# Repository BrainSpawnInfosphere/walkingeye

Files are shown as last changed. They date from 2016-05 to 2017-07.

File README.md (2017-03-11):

# XL-320 Quadruped





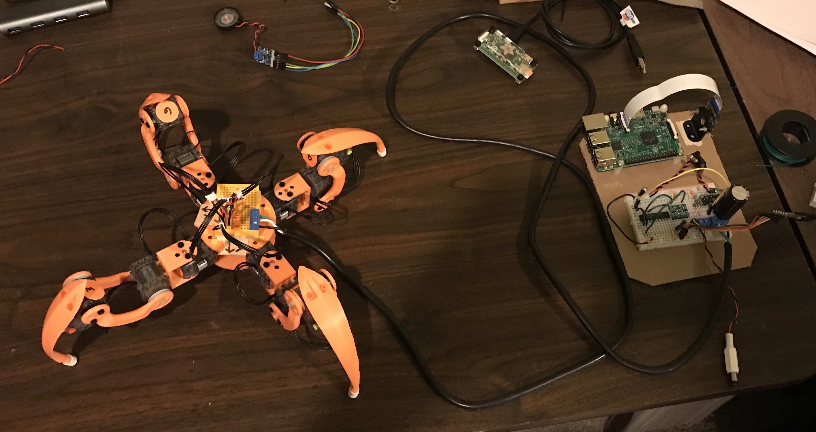
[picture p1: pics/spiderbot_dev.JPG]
spidebot dev


This is my second one after the RC version, which didn't work as nicely as I
wanted it too.

Inspired by the original [Walking Eye](https://www.youtube.com/watch?v=f77gw2Pp3aY)

## Videos

* [YouTube](https://www.youtube.com/watch?v=kH2hlxUfCNg)
* [Vimeo](https://player.vimeo.com/video/194676675)

**Still a work in progress**

## Current Pics

**As of 2017 Feb 26**

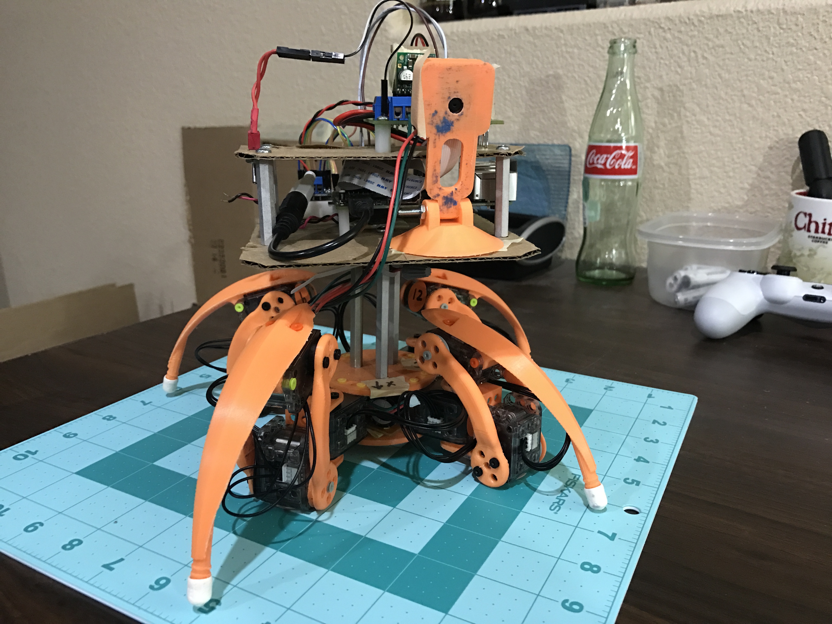
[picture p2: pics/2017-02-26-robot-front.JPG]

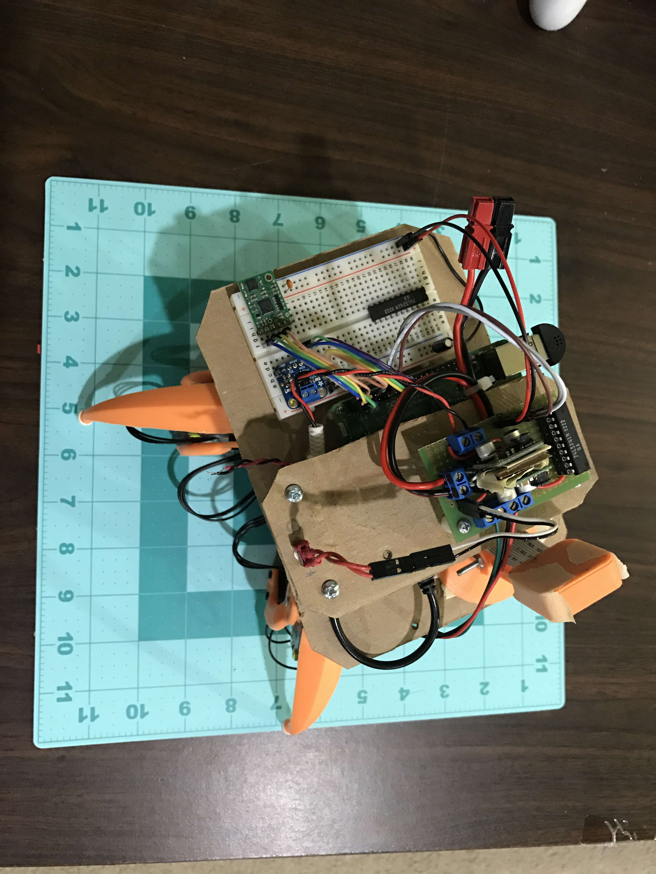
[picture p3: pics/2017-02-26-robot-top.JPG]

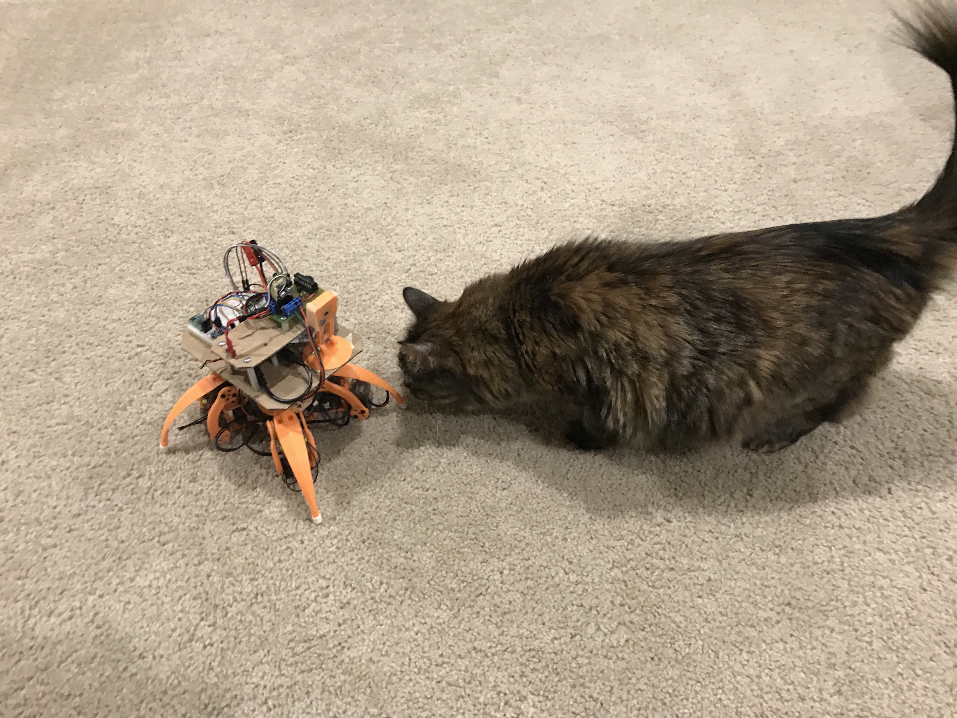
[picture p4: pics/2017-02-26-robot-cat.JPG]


Between the mat with a grid in inches and my cat, you can get an idea of the size.

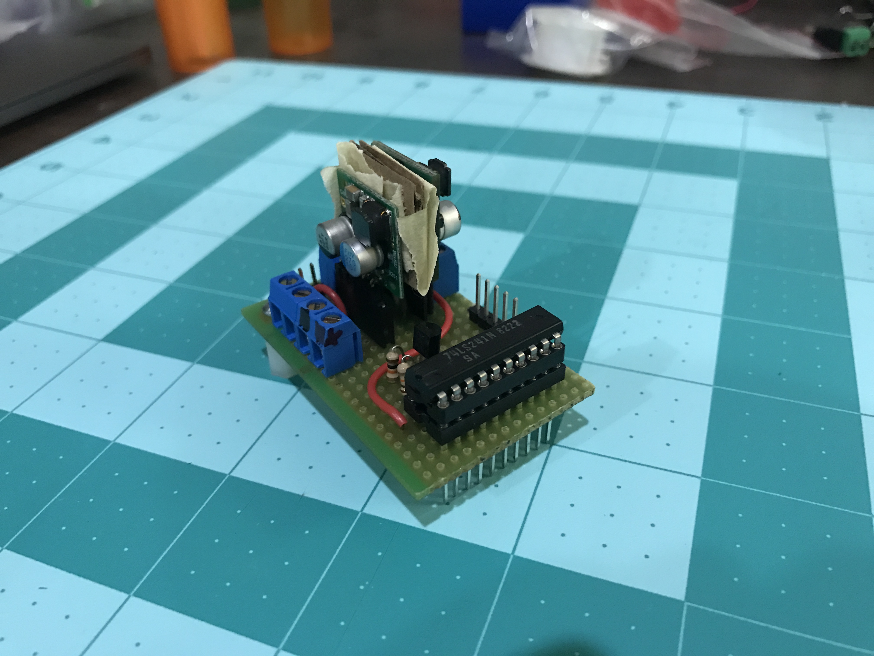
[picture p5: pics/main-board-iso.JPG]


The 2 buck converts (5V and 7.5V) were really close to each other, so I stuck a piece of cardboard between them. To prevent the cardboard from slipping, I also used some tape to hold them in place. I will eventaully turn this into a real PCB once I am fully happy with it and do a better layout.

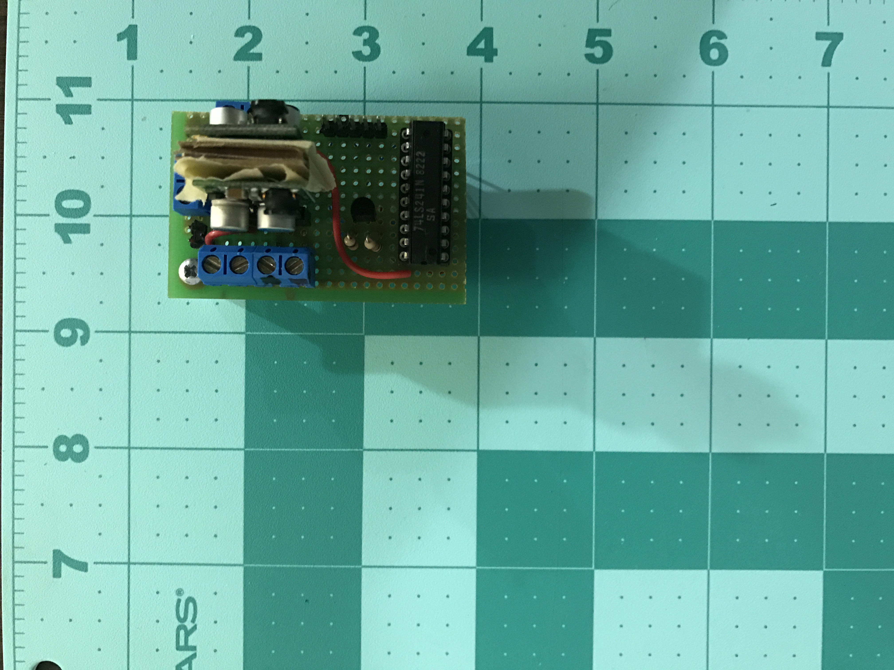
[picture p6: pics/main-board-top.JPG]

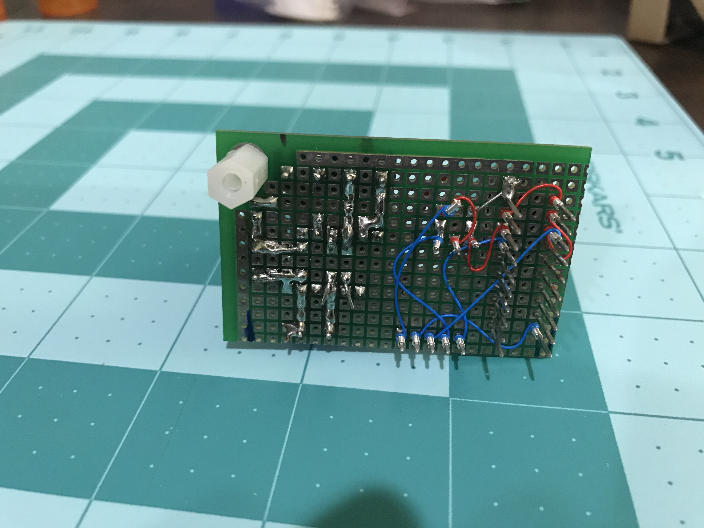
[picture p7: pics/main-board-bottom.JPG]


Decent job of soldering and wire wrapping, however, the scrap of protoboard I was useing only had 1 mounting hole to put a nylon stand off in. So far the single mount point doesn't seem to be an issue.

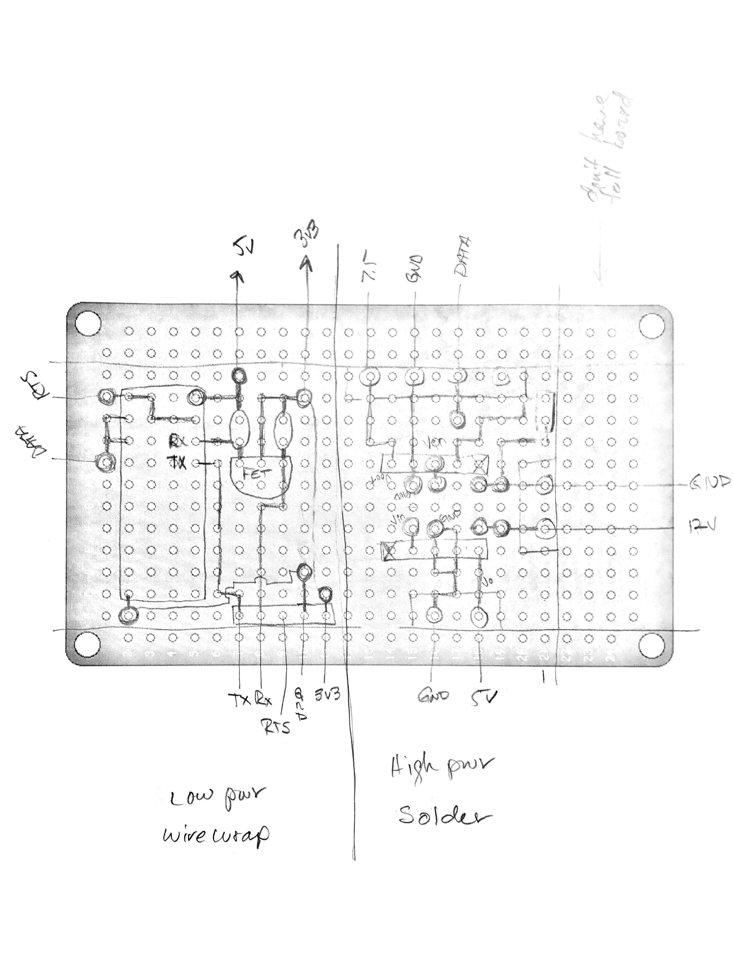
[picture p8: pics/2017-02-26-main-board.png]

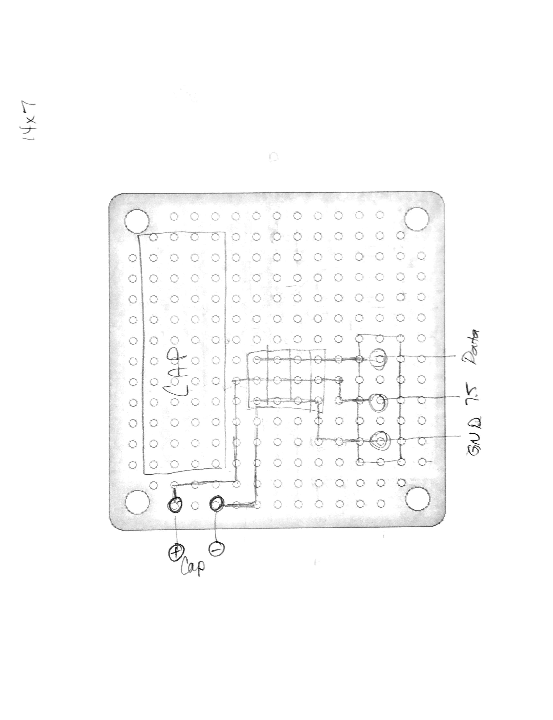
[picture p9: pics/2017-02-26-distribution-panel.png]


My hand drawn circuit diagrams using some protoboard pictures I found on the internet. I will eventually turn these into PCB's and post the schematics (probably going to use EagleCAD since it is free).

## Documentation

- [Markdown](./docs/Markdown)
- [Jupyter Notebooks](./docs/ipython)

# Licenses

**Note:** The software, hardware, and documentation are under different licenses.

## Software

**The MIT License (MIT)**

Copyright (c) 2016 Kevin J. Walchko

Permission is hereby granted, free of charge, to any person obtaining a copy of
this software and associated documentation files (the "Software"), to deal in
the Software without restriction, including without limitation the rights to
use, copy, modify, merge, publish, distribute, sublicense, and/or sell copies
of the Software, and to permit persons to whom the Software is furnished to do
so, subject to the following conditions:

The above copyright notice and this permission notice shall be included in all
copies or substantial portions of the Software.

THE SOFTWARE IS PROVIDED "AS IS", WITHOUT WARRANTY OF ANY KIND, EXPRESS OR
IMPLIED, INCLUDING BUT NOT LIMITED TO THE WARRANTIES OF MERCHANTABILITY, FITNESS
FOR A PARTICULAR PURPOSE AND NONINFRINGEMENT. IN NO EVENT SHALL THE AUTHORS OR
COPYRIGHT HOLDERS BE LIABLE FOR ANY CLAIM, DAMAGES OR OTHER LIABILITY, WHETHER
IN AN ACTION OF CONTRACT, TORT OR OTHERWISE, ARISING FROM, OUT OF OR IN
CONNECTION WITH THE SOFTWARE OR THE USE OR OTHER DEALINGS IN THE SOFTWARE.

## Hardware and Documentation

<p align="center">
	<a rel="license" href="http://creativecommons.org/licenses/by-sa/4.0/">
		
	</a>
	<br />This work is licensed under a <a rel="license" href="http://creativecommons.org/licenses/by-sa/4.0/">Creative Commons Attribution-ShareAlike 4.0 International License</a>.
</p>

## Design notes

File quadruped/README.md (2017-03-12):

# Software

**Issue:** Anything that has opencv in it *can't* be derived from `process`, opencv
crashes. It has to be in it's own python script *or* be derived from `object`.

Simple layout of the code:

- ImageServer:
	- allows image processing to be done off-board
		- allows commands to also come from a completely different type of input
		(joystick) without robot modification
	- grabs image
	- searches for:
		- tennis ball
		- people's faces
	- publishes:
		- images
		- commands to robot

- Audio:
	- listen for speach
	- convert to wave format
	- send to service (wit or whatever)
	- 

- Quadruped:
	- Engine({serial})
	- AHRS() - compass
	- MCP3208() - ADC for IR and whatever else
	- movement_states['walk', 'climb', 'animate', 'sit', 'stand']
		- these are used to call movements[] functions using command()
	- movements[]
		- Gait:
			- command(x, func_move_foot) - moves all feet through 1 gait cycle (12 steps)
			- eachLeg(x,y,z)
		- Pose:
			- command(func_move_foot) - sends all feet through an animation sequence to final position
			- eachLeg(x,y,z)

- Engine({serial}): - handles movement hardware
	- legs[4]
		- servos[3]
			- angle
			- setServoLimits()
			- bulkWrite() - change to sync
		- coxa, femur, tibia
		- fk()
		- ik()
		- moveFoot(x,y,z)
		- moveFootAngle(a,b,c)
	- moveFoot(x,y,z) - gaits need a function to call

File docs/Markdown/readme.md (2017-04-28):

# Documentation

**This is still a work in progress**

This documentation is broken up into two types:

- Static markdown files
- Interactive python files (Jupyter notebooks)

Since the software is written in python, iPhython (or now
[Jupyter](http://jupyter.org/)) is used for interactive documentation. Take a
look at the [docs](https://github.com/walchko/WalkingEye/tree/master/docs/ipython)
folder. The ipython files are where some of the development (e.g., gait,
forward/inverse kinematics, etc) takes place before it is tranferred into the
python code.

When viewing the notebooks on `github.com`, they are static, but if you download
them and have Jupyter installed, they are interactive and pretty cool.

## Index

- [Software](./software.md)
- [Hardware](./bom.md)
- [Power](./power.md)
- [History](./history.md)

---

<p align="center">
	<a rel="license" href="http://creativecommons.org/licenses/by-sa/4.0/">
		
	</a>
	<br />This work is licensed under a <a rel="license" href="http://creativecommons.org/licenses/by-sa/4.0/">Creative Commons Attribution-ShareAlike 4.0 International License</a>.
</p>

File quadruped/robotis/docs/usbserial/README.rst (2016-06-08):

USB Serial
=============



RPi v3: ``/dev/tty.????``
OSX: ``/dev/tty.usbserial``

PmodUSBUART Pinout
-------------------------

=== ====== ===========================
Pin Signal Description
=== ====== ===========================
1   RTS    Ready to Send
2   RXD    Receive
3   TXD    Transmit
4   CTS    Clear to Send
5   GND    Ground
6   3V3    Power
=== ====== ===========================

Other
----------

=== === ======================================================

=== === ======================================================
JP1 SYS Powered by FTDI chip, supplies power to remote board
JP1 LCL If remote board is powered, use this setting
LED 1   Data transfer from host computer USB to UART
LED 2   Data transfer from UART to host computer USB
=== === ======================================================

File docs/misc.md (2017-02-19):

Name:   mcp23017
Info:   Configures the MCP23017 I2C GPIO expander
Load:   dtoverlay=mcp23017,<param>=<val>
Params: gpiopin                 Gpio pin connected to the INTA output of the
                                MCP23017 (default: 4)

        addr                    I2C address of the MCP23017 (default: 0x20)

Name:   i2s-gpio28-31
Info:   move I2S function block to GPIO 28 to 31
Load:   dtoverlay=i2s-gpio28-31
Params: <None>

Name:   i2c1-bcm2708
Info:   Enable the i2c_bcm2708 driver for the i2c1 bus
Load:   dtoverlay=i2c1-bcm2708,<param>=<val>
Params: sda1_pin                GPIO pin for SDA1 (2 or 44 - default 2)
        scl1_pin                GPIO pin for SCL1 (3 or 45 - default 3)
        pin_func                Alternative pin function (4 (alt0), 6 (alt2) -
                                default 4)

Name:   i2c-rtc
Info:   Adds support for a number of I2C Real Time Clock devices
Load:   dtoverlay=i2c-rtc,<param>=<val>
Params: ds1307                  Select the DS1307 device

        ds1339                  Select the DS1339 device

        ds3231                  Select the DS3231 device

        mcp7940x                Select the MCP7940x device

        mcp7941x                Select the MCP7941x device

        pcf2127                 Select the PCF2127 device

        pcf8523                 Select the PCF8523 device

        pcf8563                 Select the PCF8563 device

        trickle-resistor-ohms   Resistor value for trickle charge (DS1339-only)

        wakeup-source           Specify that the RTC can be used as a wakeup
                                source

Name:   i2c-pwm-pca9685a
Info:   Adds support for an NXP PCA9685A I2C PWM controller on i2c_arm
Load:   dtoverlay=i2c-pwm-pca9685a,<param>=<val>
Params: addr                    I2C address of PCA9685A (default 0x40)

Name:   i2c-mux
Info:   Adds support for a number of I2C bus multiplexers on i2c_arm
Load:   dtoverlay=i2c-mux,<param>=<val>
Params: pca9542                 Select the NXP PCA9542 device

        pca9545                 Select the NXP PCA9545 device

        pca9548                 Select the NXP PCA9548 device

        addr                    Change I2C address of the device (default 0x70)

Name:   i2c-gpio
Info:   Adds support for software i2c controller on gpio pins
Load:   dtoverlay=i2c-gpio,<param>=<val>
Params: i2c_gpio_sda            GPIO used for I2C data (default "23")

        i2c_gpio_scl            GPIO used for I2C clock (default "24")

        i2c_gpio_delay_us       Clock delay in microseconds
                                (default "2" = ~100kHz)

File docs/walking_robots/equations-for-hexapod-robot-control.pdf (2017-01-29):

Equations for hexapod robot control | www.hexapod-kit.com

# Equations for Hexapod robot control

Determine joints angles according to the position of leg tip. A method for linear interpolation (straight walk).
A method for circular interpolation (curved walk).
A method for body inclination (tilt).

Determine joints angles according to the position of leg tip.

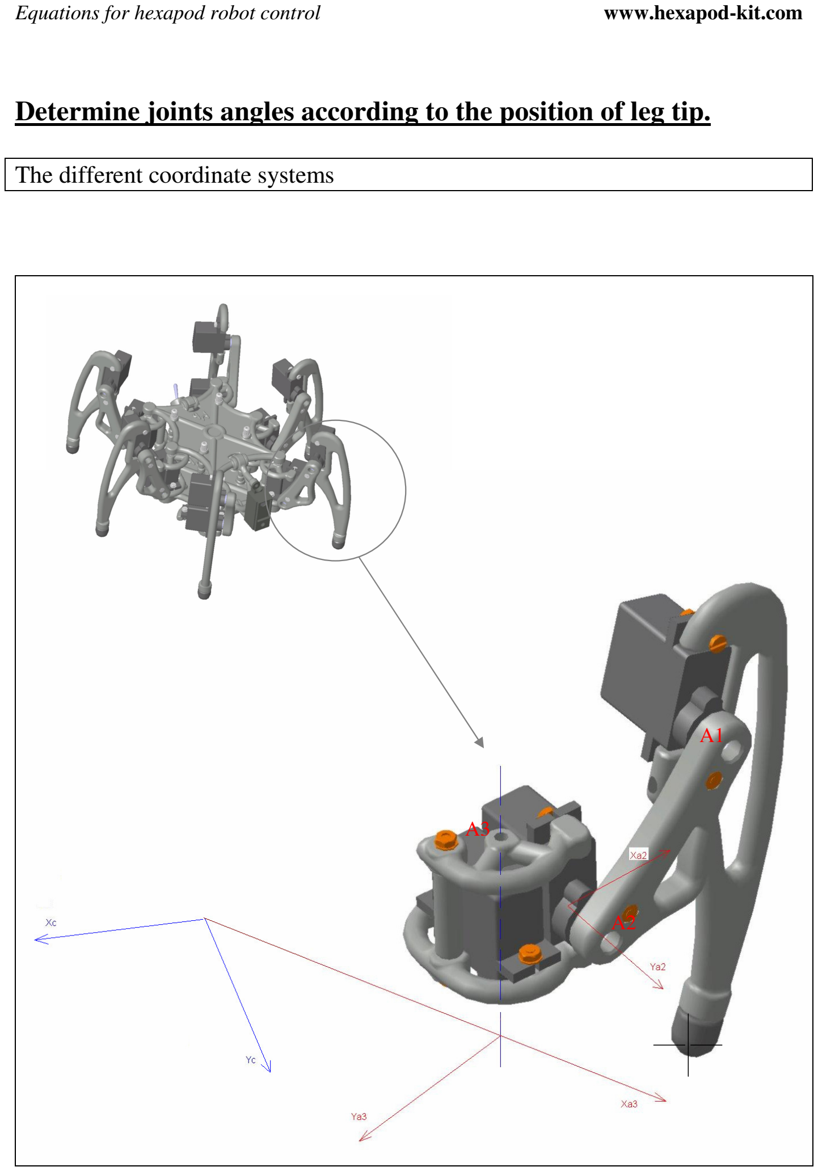
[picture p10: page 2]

The different coordinate systems

A1

A2

A3

We want to drive the tip of a leg by its coordinates in a Cartesian coordinate system.
For reasons of simplicity, we express the coordinates in a fixed coordinate system centred on the body of the hexapod.
To calculate the angles to be applied to the three joints of the leg we have to use different coordinate systems, either fixed or movable relative to the body.
All angle measurements in formulas are expressed in radians.
- Coordinate systems fixed to the body c et a3 :

Seen from above

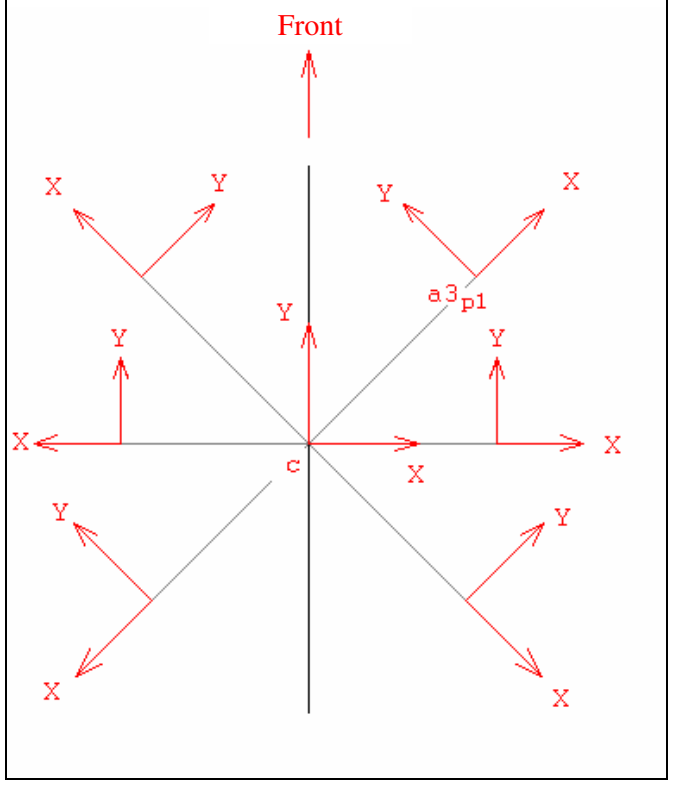
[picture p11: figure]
Front

System c is centred on the robot body. The plan [XY] of the system coincides with the underside of the body (the lowest point).
Systems a3px are centred on A3 joints of each leg.

- Coordinate systems movable relative to the body a2:

Seen top

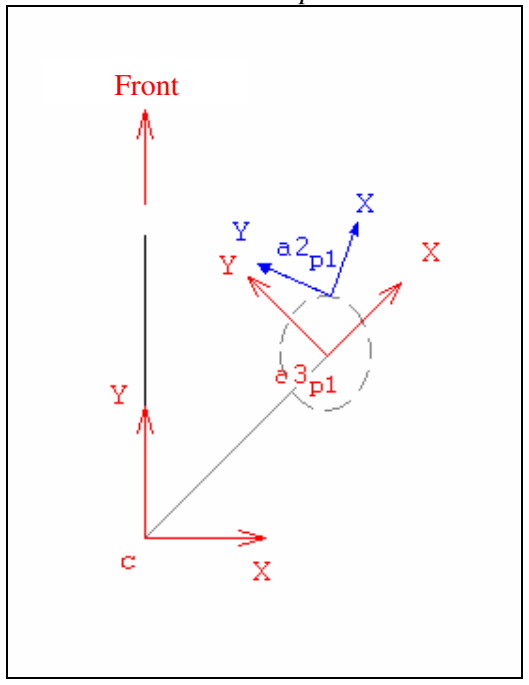
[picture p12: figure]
Front

Joints A2 and A1 in the [XZ] plan of coordinate system a2 :

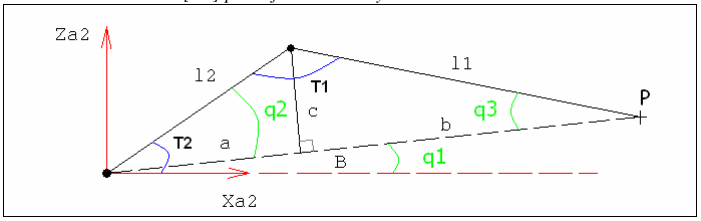
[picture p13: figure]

Given :

- l1et l2 respectively the lengths of the extreme and middle phalanxes.
- T1 angle between the extreme phalanx and middle phalanx.
- T2 angle between X axis and the middle phalanx.
- q1 angle between the axis X and B imaginary line passing through the joint centre A2 and the point P.
- q2 angle between B and the middle phalanx.
- q3 angle between B and the extreme phalanx.

B = a + b
2 | 2 | 2 B = Pxa2 + Pza2

2

cos( )2
l

a
q =

T 2 = q1+ q2

Find T2

B

B | l | l
a
B | aB | l | l
a | B | a | aB | l | l
a | B a | l | l
a | b | l | l
b | l | c
a | l | c

2

2 1

2 | 2 | 1
( | 2 | ) | 2 | 1
( | ) | 2 | 1

2 1

1

2

2 | 2 | 2
2 | 2 | 2
2 | 2 | 2 | 2 | 2
2 | 2 | 2 | 2
2 | 2 | 2 | 2
2 | 2 | 2
2 | 2 | 2
+ | −
=
− | + | = | −
− | + | − | = | −
− | − | = | −
− | = | −
= | −
= | −
l | B
B | l | l
q
2* 2*

2 1
cos( )2
2 | 2 | 2
+ | −
= | )
2

2
) arctan(
2* 2*

2 1

### 2 arccos(

2 | 2 | 2

Pxa

Pza
l | B
B | l | l
T | +
+ | −
=

)
2

2

### 1 arctan(

Pxa

Pza
q =

B

B | l | l
a
| 2 | 2 1
2 | 2 | 2
+ | −
=

cos(a −b) = cos(a)cos(b) + sin(a)sin(b)

Find T1

2 1 2

2 1
2 1 2
2 2 | 2 | 1
cos( )1
| | 2 1 2 2 2
2 1 2
| 2 1
cos( )1

1 2 1 2

2
1 2

2
cos( )1

1 2

2 | ( ( | ))
2
2 | ( | )
cos( )1

1 2

2
1 2

cos( )1

1 1 2

*
2

cos( )1

1 1 2

*
2

cos( )1

1 1 2

1
*
2

2
cos( )1

1 1 2

* 1
2

cos( )1 1

1 2

))
1

*) arcsin(
2

cos( )1 cos(arcsin(

)
1

) arcsin(
2

### 1 arcsin(

) )
1

) arcsin(
2

1 ( arcsin(

)
1

) arccos(
2

### 1 arccos(

1 | 2 | 3
2 | 2 | 2 | 2 | 2 | 2 | 2
2 | 2 | 2 | 2

2 2

2

2

2 2

2 | 2 | 2

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
l | l | B
l l
l | B | l | l
T

ll

l
ll
B | l | l
T

ll

aB
ll

l
ll

l aB T

ll

l a a b
l
l | a | ab T

ll

l | a | ab
ll

c ab T

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
T | q | q
+ | −
=
− | − | +
=
| | +
+ | −
= −
= | −
− | +
= −
− | + | +
= −

− −
=

− +
=

+
=
= | +
= | +

+

− | −
=
= | − | − | +
= | +
= | −
= | − − | + | +
= | − | −
= | − | −
π | π

π

π

)
2 1 2

1 2

### 1 arccos(

2 | 2 | 2

l l

l | l | B
T

+ −
=

Find joint angle A3 (T3)

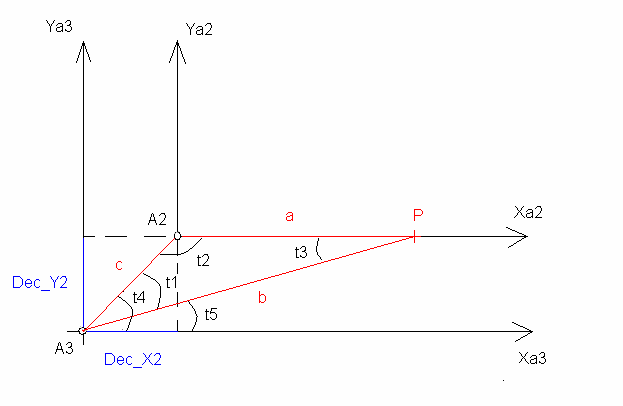
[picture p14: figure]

- Dec_X2 is the offset on X axis, between joints A3 et A2.
- Dec_Y2 is the offset on Y axis, between joints A3 et A2.
- Dec_Z2 is the offset on Z axis, between joints A3 et A2 (=0).
- Given a the projection on Xa2 of the imaginary line B (seen previously).

2 2

2 2

3 3

)
_ 2

_ 2
arctan(
2

2

_ 2 | _ 2
b | Pxa | Pya Dec Y

Dec X
t
c | Dec X | Dec Y
= | +
= | +
= | +

π

We know that :

sin( )1 | sin( )2 | sin(t )3 c
| t

b
t

a
= | = | Sinus proportionality rule.

So :

sin( )2 | cos( )2 )

sin( )2
1 2 arcsin(

)

sin( )2

### 3 arcsin(

2 | 2 | 2
a | b | c | t | c | t

b

c | t
t | t

b

c t
t
= | − | × | + ×

×
= | − | −
| | ×
=

π

2 | sin( )2 | cos( )2
2 | 2 | 2 Pxa = Bx = b − c × | t | + c × | t

Pya2 = 0

)
3

3

### 5 arctan(

)

sin( )2

### 1 arcsin(

)
_ 2

_ 2

### 4 arctan(

Pxa

Pya
t

b

a t
t

Dec X

Dec Y
t

=

×
=

=

Given T3 the angle of the joint A3, we have :

T3 = t5 + t1− t4

Change of coordinate system (system c to a3)

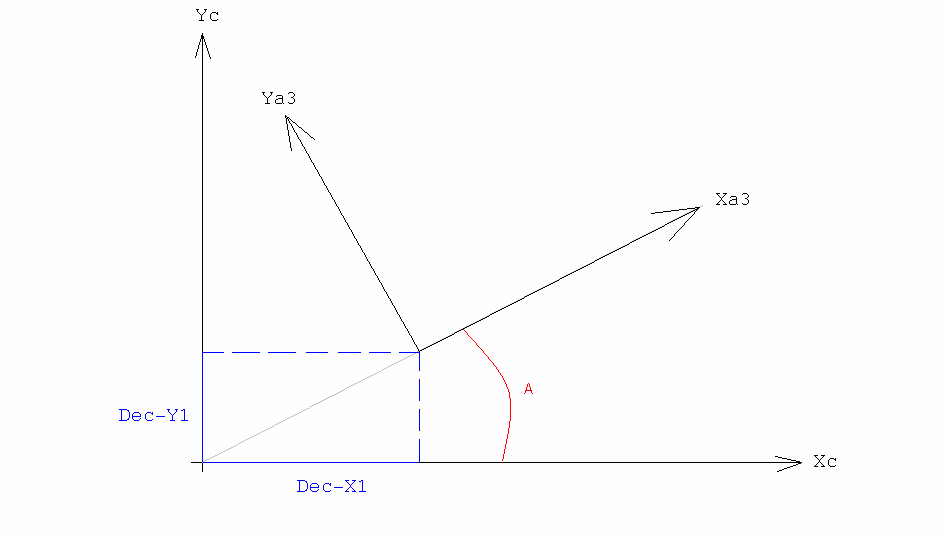
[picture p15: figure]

- System a3 is centred on A3 joint.
- System c is centred on the hexapod body (Y axis pointing to the front of the hexapod).
- A is the angle between X axis of the body centred system and the X axis of the A3 joint centred system.
- Dec_X1 is the abscissa of a3 system centre, expressed in the c system.
- Dec_Y1 is the ordinate of a3 system centre, expressed in the c system.
- Dec_Z1 is the altitude of a3 system centre, expressed in the c system (=0).

A, Dec_X1, Dec_Y1 et Dec_Z1 are not the same for all legs.

3 | ( | cos( ) | sin( ))
3 | cos( ) | sin( ) | _ 1 | _ 1

2 2

Pya | Pyc | A | Pxc | A
Pxa | Pxc | A | Pyc | A | DEC X | DEC Y
= − | × | − | ×
= | × | + | × | − | +

Sum up

Coordinate system c to a3 :

### 3 _ 1

3 | ( | cos( ) | sin( ))
3 | cos( ) | sin( ) | _ 1 | _ 1

2 2

Pza | Pzc Dec Z
Pya | Pyc | A | Pxc | A
Pxa | Pxc | A | Pyc | A | DEC X | DEC Y
= | −
= − | × | − | ×
= | × | + | × | − | +

Coordinate system a3 to a2 :

2 | 3 | _ 2

2 0

2 | sin( )2 | cos( )2
| ) _ 2

_ 2
arctan(
2

2

3 3

_ 2 | _ 2
2 | 2 | 2

2 2

2 2

Pza | Pz | Dec Z

Pya

Pxa | Bx | b | c | t | c | t
| | | Dec Y

Dec X
t
c | Pxa | Pya
b | Dec X | Dec Y
= | −

=

= | = | − | × | + ×
= | +
= | +
= | +

π

Joints angles :

2 2 B = Pxa2 + Pza2

)
2 1 2

1 2

### 1 arccos(

2 | 2 | 2

l l

l | l | B
T

+ −
=

)
2

2
) arctan(
2* 2*

2 1

### 2 arccos(

2 | 2 | 2

Pxa

Pza
l | B
B | l | l
T | +
+ | −
=

)
_ 2

_ 2
) arctan(
3 3

))
_ 2

_ 2
arctan(
2

sin(
) arcsin(
3

3

### 3 arctan(

2 | 2 | Dec X Dec Y
Pxa | Pya
| Dec Y

Dec X
a

Pxa

Pya T | −

+

× | +
= | +

π

A method for linear interpolation (straight walk).

Straight walking consist in moving with a given distance in a given direction with a given step.

The three method parameters are :

L : The distance.
A : Angle between walking direction and the longitudinal axis of the hexapod (Yc). P : The unitary step of the leg (linear distance made in one walking cycle).

Another parameter is also used :

G : The ground clearance (body to ground distance).

Example for leg n°1

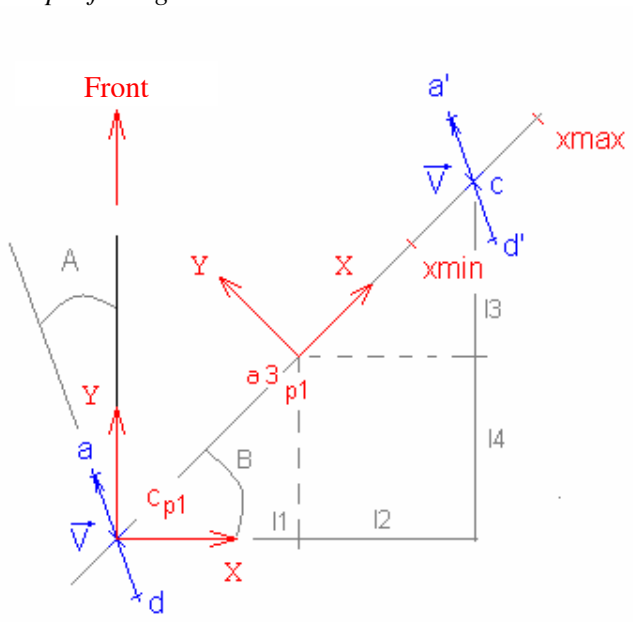
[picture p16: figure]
Front

Given V

r
the vector which norm is equal to L, and which angle with Yc axis is A .

### 4 _ 1

)
2

max min 3 sin( ) ( min

)
2

max min 2 cos( ) ( min

### 1 _ 1

l | Dec Y
x | x
l | B | x
x | x
l | B | x
l | Dec X

=

−
= | × | +

−
= | × | +

=

Coordinates of starting and arrival points d et a expressed in cp1 system.

dy | ay
dx | ax

L
ay | A

L
ax | A

= −

= −

= | ×
= − | ×

2

cos( )

2

sin( )

Coordinates of starting and arrival points d’ et a’ translated on c point expressed in cp1 system.

' | 3 | 4
' | 1 | 2
' | 3 | 4
' | 1 | 2
d y dy l | l
d x dx l | l
a y ay l | l
a x ax l | l
= | + | +
= | + +
= | + | +
= | + +

Then, we are able to calculate the values of the different joints for starting and arrival point thanks to the previous formulas.

Remarks :

Leg movement vector points in the opposite direction to the wanted body movement vector.

Number of cycles to be performed to reach the distance is equal to
P

L

In cp1 system Z coordinate of the leg tip is equal to –G.

A method for circular interpolation (curve walk).

Curve walking consists in moving of a given angle on a circle of given centre with a given step.

The three method parameters are :

A : Rotation angle.
C(xc;yc) : Coordinates of the rotation centre.
P : Unitary step of the leg (linear distance made in one walking cycle).

Another parameter is also used :

G : The ground clearance (body to ground distance).

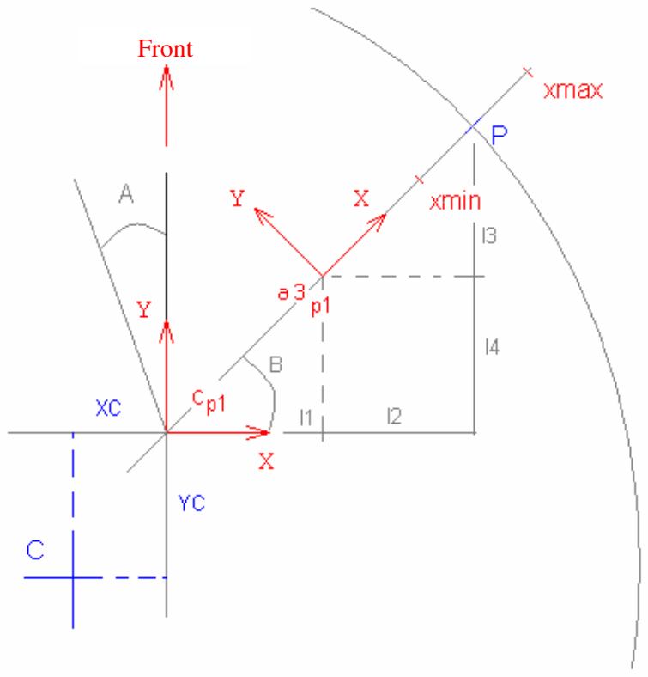
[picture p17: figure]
Front

### 4 _ 1

)
2

max min 3 sin( ) ( min

)
2

max min 2 cos( ) ( min

### 1 _ 1

l | Dec Y
x | x
l | B | x
x | x
l | B | x
l | Dec X

=

−
= | × | +

−
= | × | +

=

Compared to straight walking not all legs have the same movement vector. For a given unitary angular step, the farthest leg from the rotation centre will describe the longest distance in one walking cycle (Equal to P in our case).

At first we have to determine which leg is the farthest from the rotation centre.
For each leg we calculate the length of CP segment :
( | ) ( | ) ² | 2
CP = | l1+ l2 − XC + l3 + l4 −YC

For the leg which have the maximal CP, we calculate the angle T represented by points a and d spaced of a distance P, belonging to the circle.

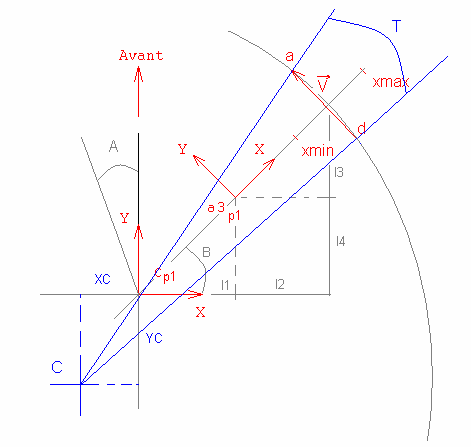
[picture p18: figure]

CP

P
T

Circ

P
T
Circ | CP

=

× ×
=

= × ×

π

π
2

2

T will be the unitary angular step for all legs in order to respect the unitary linear step P.

In the coordinate system centred on the cercle we express :

- The angle between the starting point d and X axis :
( | )
( | ) | 2

)
1 2

3 4
arctan( | T
l | l | XC
l | l | YC Ad | −
+ | −
+ | −
=
- The angle between the arrival point a and X axis :
( | )
( | ) | 2

)
1 2

3 4
arctan( | T
l | l | XC
l | l | YC Aa | +
+ | −
+ | −
=
- d and a coordinates :
Ya | Aa | CP
Xa | Aa | CP
Yd | Ad | CP
Xd | Ad | CP
= | ×
= | ×
= | ×
= | ×
sin( | )
cos( | )
sin( | )
cos( | )

Now we can calculate the coordinates in the body coordinate system of the starting and arrival movement vector points.

Ya | Aa | CP | YC
Xa | Aa | CP | XC
Yd | Ad | CP | YC
Xd | Ad | CP | XC
= | × | +
= | × | +
= | × | +
= | × | +
(sin( | ) | )
(cos( | ) | )
(sin( | ) | )
(cos( | ) | )

Then, we are able to calculate the values of the different joints for starting and arrival point thanks to the previous formulas.

## A method for body inclination (tilt)

Inclination consists in tilting the body of the robot of a given angle A around the longitudinal axis and a given angle B around the transversal axis.
Thus we must have the six leg extremity belonging to the same plane, tilted of the desired value relative to [XY] body plan.

The three method parameters are :

A : rotation angle around Y.
B : rotation angle around X.
G : The ground clearance (body to ground distance).

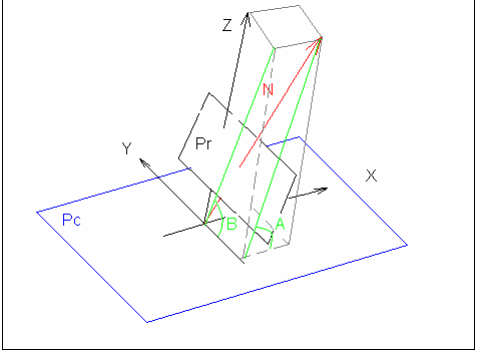
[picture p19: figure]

Calculation of the vector N normal to the Pr plan (tilted plan)

Z | Z | 1

Y Y Z/tan(B)

X X Z/tan(A)

=

=

=
N =

r

Coordinates of the body coordinate system centre projected to the Pr plan, expressed in the body coordinate system.

P = (0;0;-G)

Plane equation.

Given:

N {a,b,c} vector normal to the plan.
A {xa,ya,za} a known point belonging to the plan. M {x,y,z} a point belonging to the plan.
The plan equation is : ax+by+cz - (axa+bya+cza) = 0

If d=(axa+bya+cza) is the constant part of the equation.
In our case d=-G

Calculation of the coordinates of a leg tip in the body coordinate system.

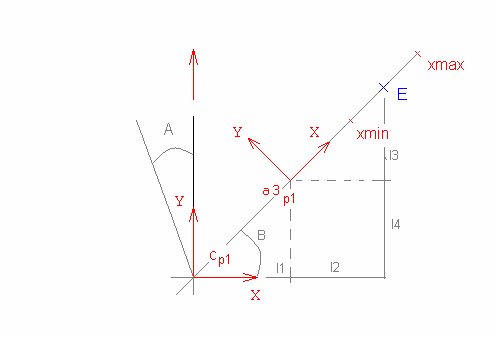
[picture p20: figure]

### 4 _ 1

)
2

max min 3 sin( ) ( min

)
2

max min 2 cos( ) ( min

### 1 _ 1

l | Dec Y
x | x
l | B | x
x | x
l | B | x
l | Dec X

=

−
= | × | +

−
= | × | +

=

)
tan( ) tan( )

(

3 4

1 2

B

Ey
A
Ex Ez | G
Ey l | l
Ex l | l
= − − | −
= | +
= | +

Then, we are able to calculate the values of the different joints for the starting and arrival points thanks to the previous formulas.

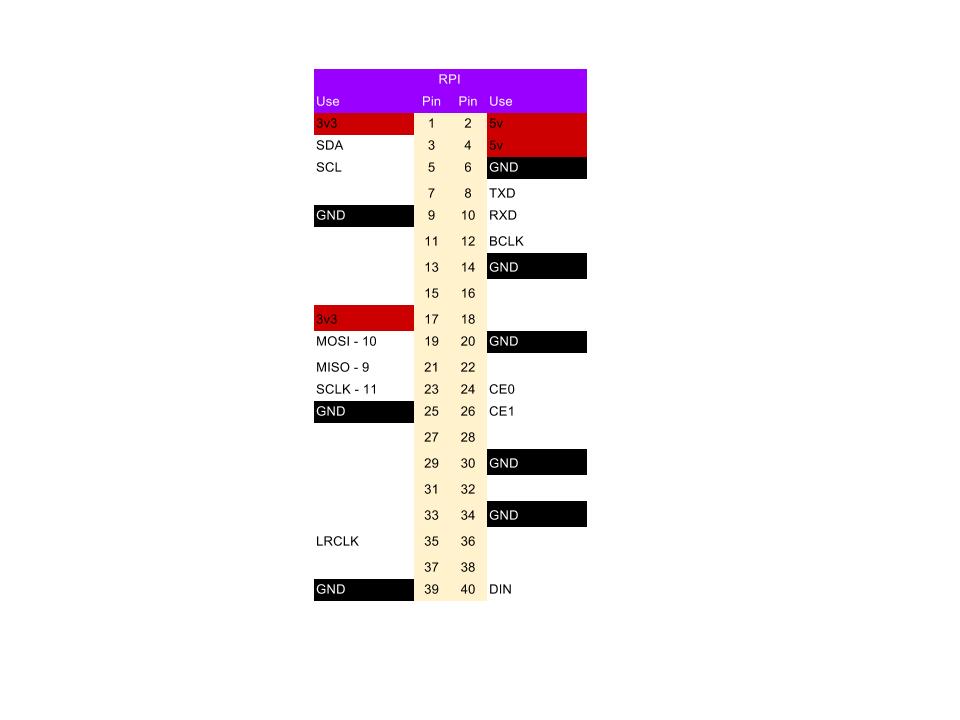
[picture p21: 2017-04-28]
docs/Markdown/pics/sider_pinout.jpg

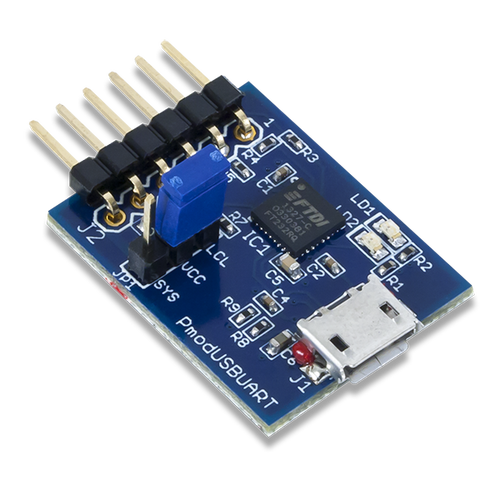
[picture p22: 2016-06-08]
quadruped/robotis/docs/usbserial/usbserial.png

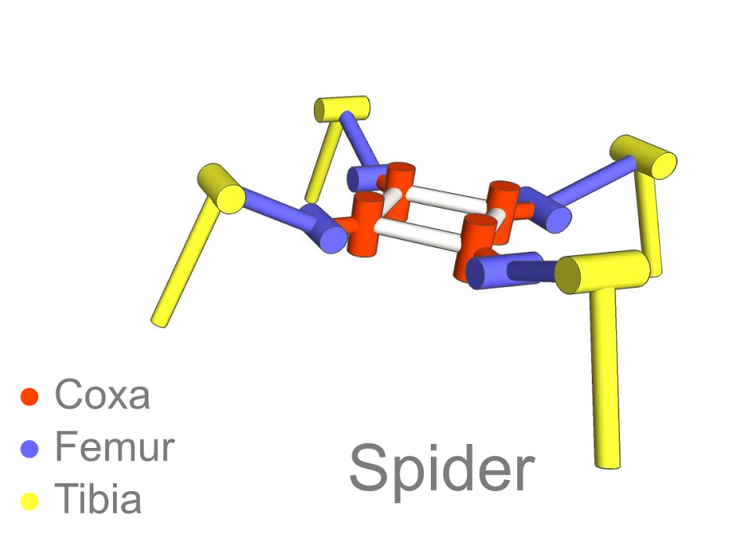
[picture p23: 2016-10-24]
docs/spider.png

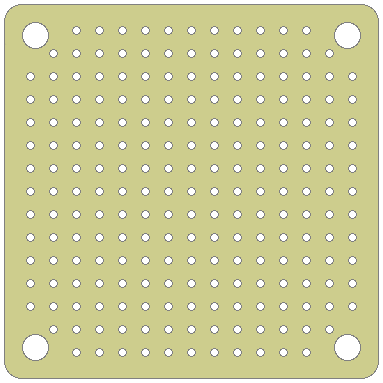
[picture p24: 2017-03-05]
docs/perf_board/small-template.png

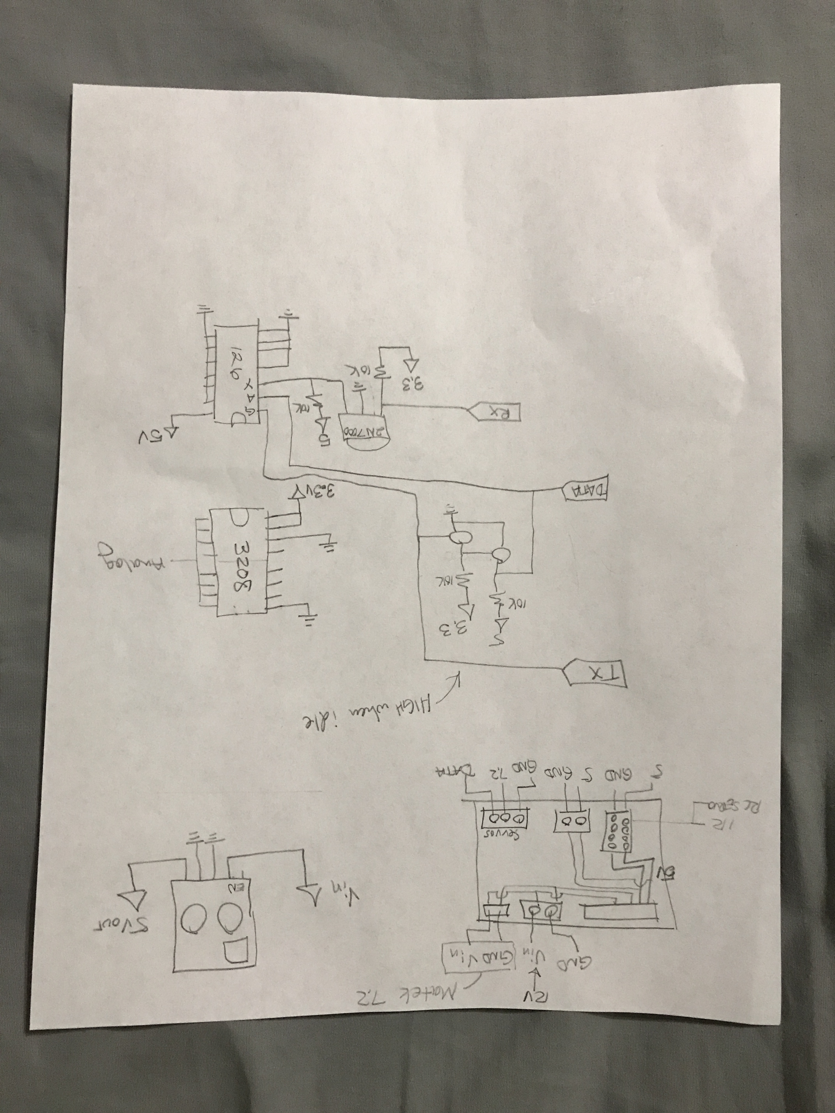
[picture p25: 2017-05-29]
docs/2017-05-09 06.19.26.jpg

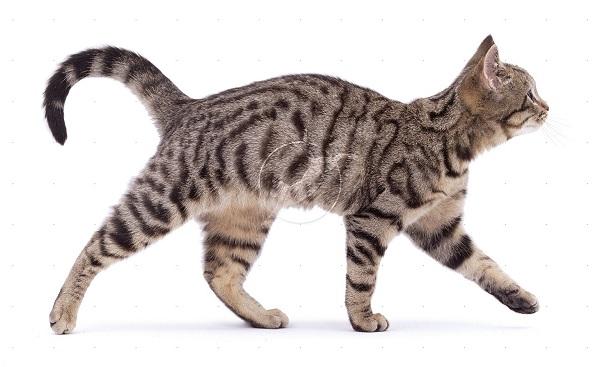
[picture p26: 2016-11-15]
pics/brown-tabby-cat.jpg

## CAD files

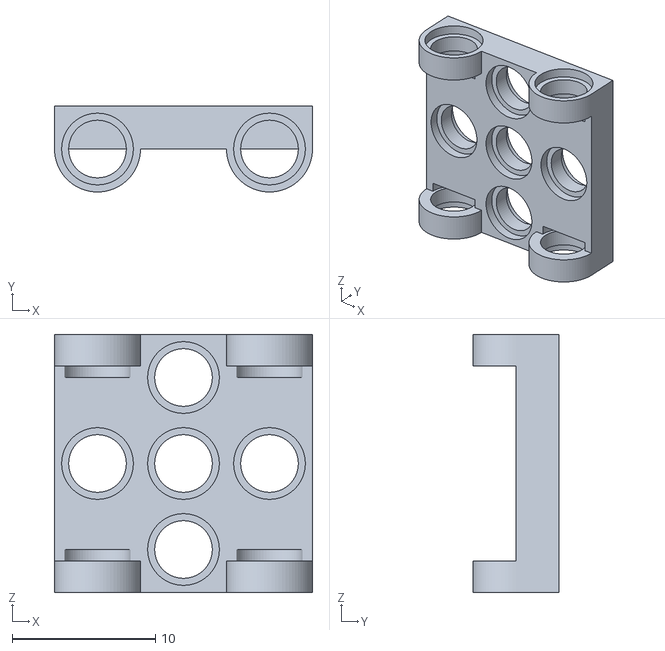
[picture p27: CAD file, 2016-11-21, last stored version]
hardware/darwin-mini/frame_adaptor.stl
18.0 x 6.00 x 18.0

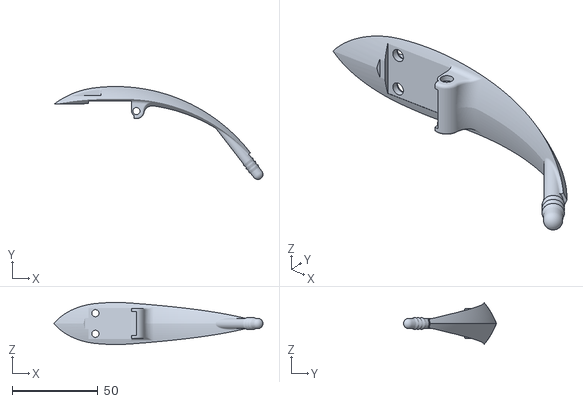
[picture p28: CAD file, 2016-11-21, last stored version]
hardware/nico/tibiaLong_SLA.STL
122.2 x 54.3 x 24.6

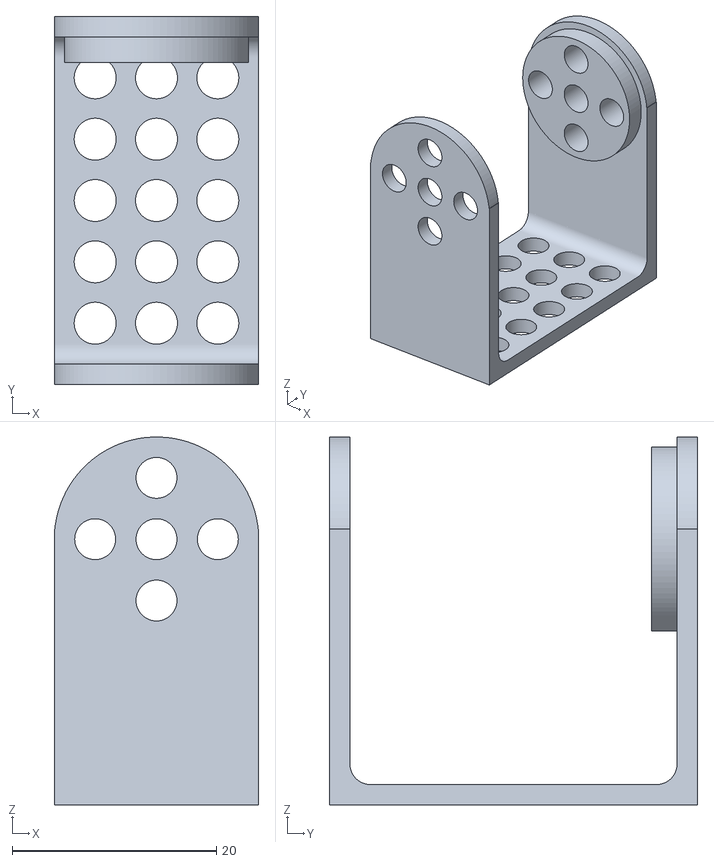
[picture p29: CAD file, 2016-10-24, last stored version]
hardware/openscad/stl/parts.stl
20.0 x 36.0 x 36.0

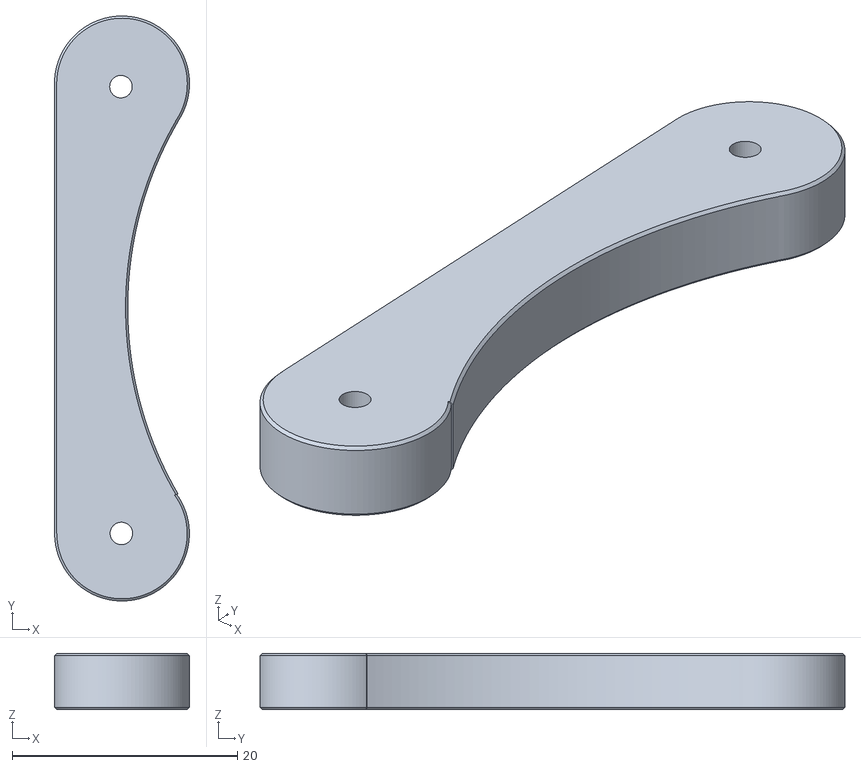
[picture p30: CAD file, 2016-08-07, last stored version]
quadruped/3d_printer/femur_v_2.stl
12.0 x 52.0 x 5.00

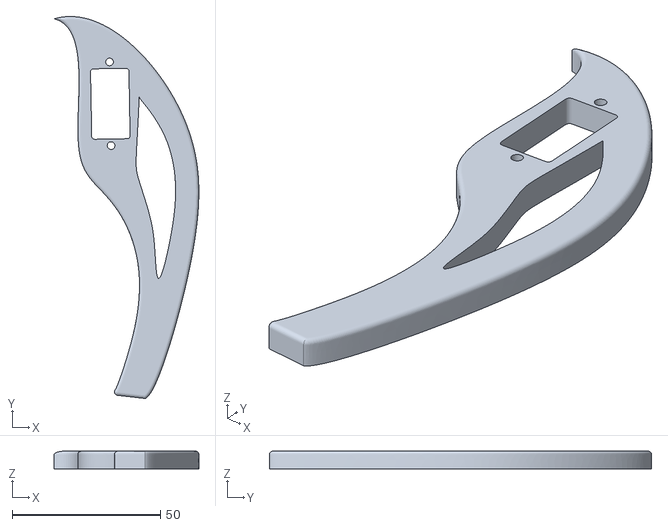
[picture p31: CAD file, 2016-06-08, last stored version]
quadruped/W4lker-master/stl/tibia3.stl
48.8 x 128.7 x 6.00

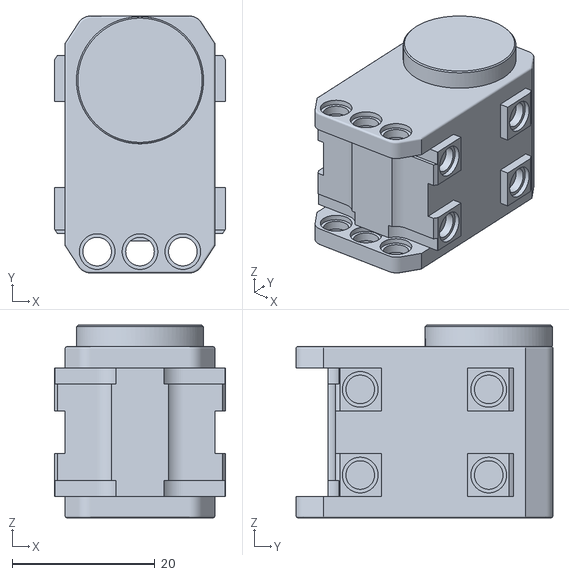
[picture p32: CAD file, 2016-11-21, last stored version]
hardware/darwin-mini/xl320_dummy.stl
24.0 x 36.0 x 27.0

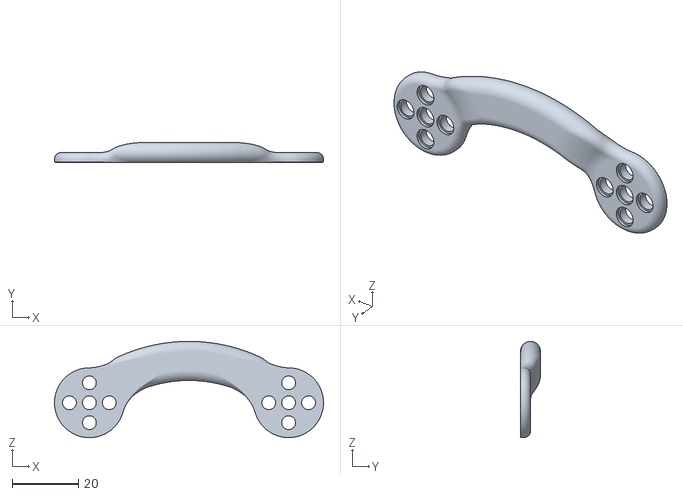
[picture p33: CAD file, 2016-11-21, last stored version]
hardware/nico/femur_SLA.STL
81.0 x 6.00 x 29.0

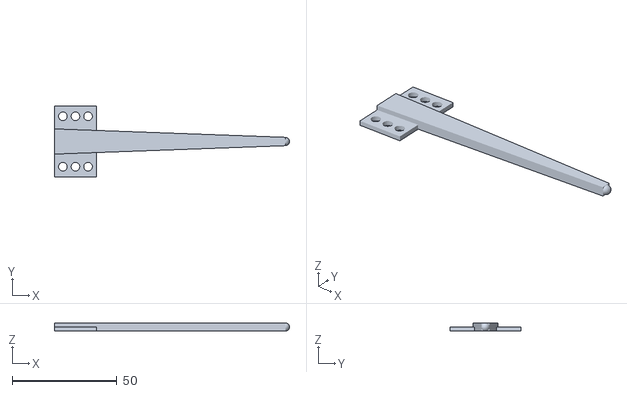
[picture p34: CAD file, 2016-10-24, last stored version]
hardware/openscad/stl/leg.stl
112.0 x 34.0 x 4.00

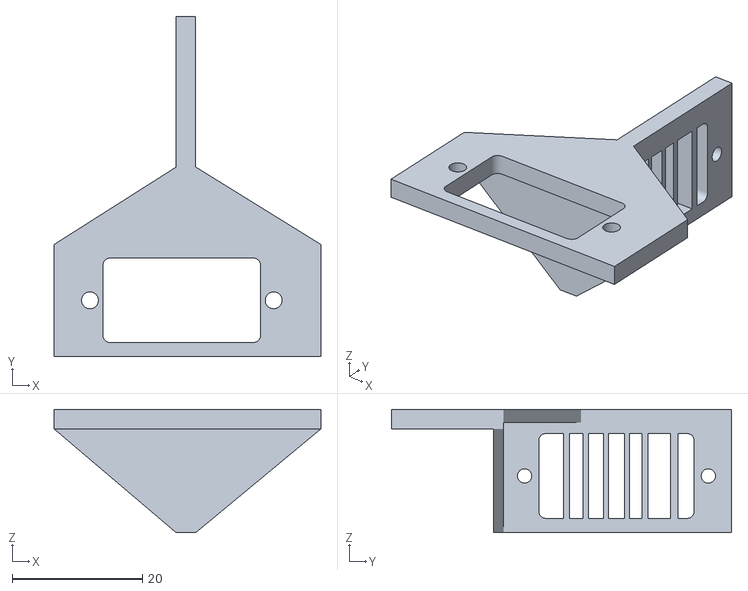
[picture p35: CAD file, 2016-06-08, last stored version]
quadruped/W4lker-master/stl/shoulder_supports.stl
41.0 x 52.2 x 18.9

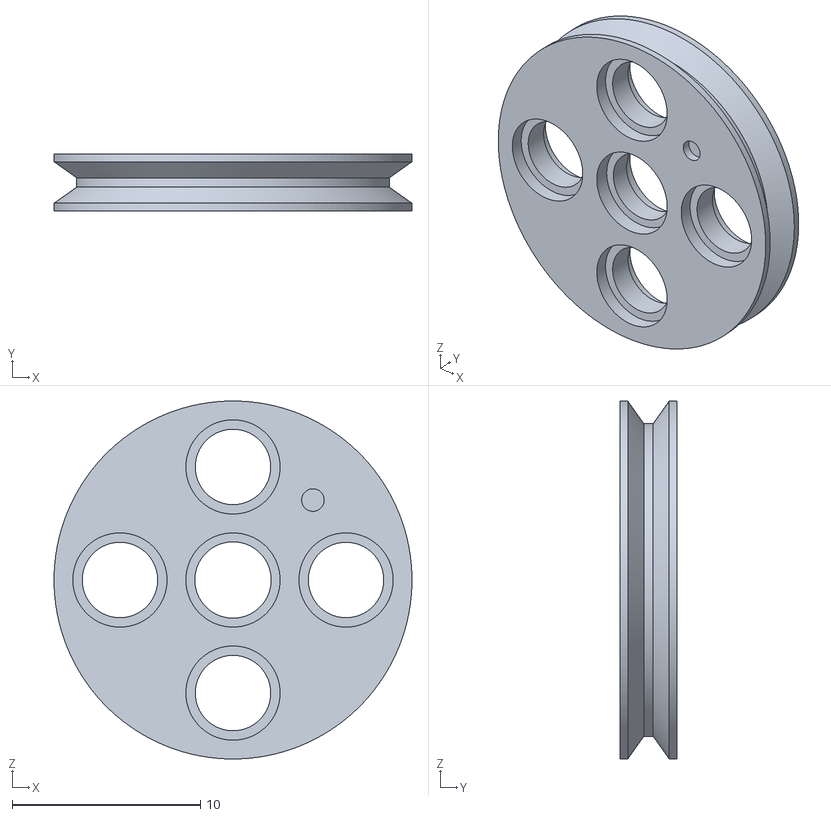
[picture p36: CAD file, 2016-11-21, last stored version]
hardware/darwin-mini/pully.stl
19.0 x 3.00 x 19.0

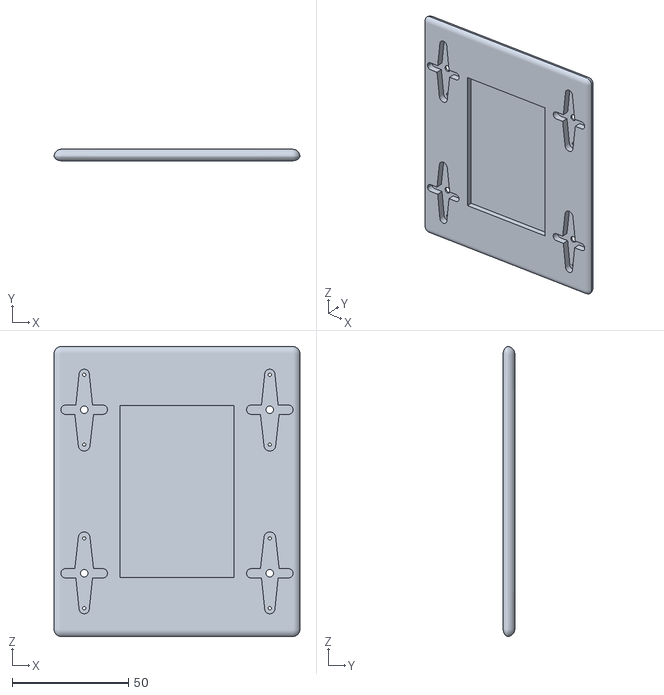
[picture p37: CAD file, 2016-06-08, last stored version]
quadruped/W4lker-master/stl/base3 filet 2.stl
106.0 x 5.00 x 125.0

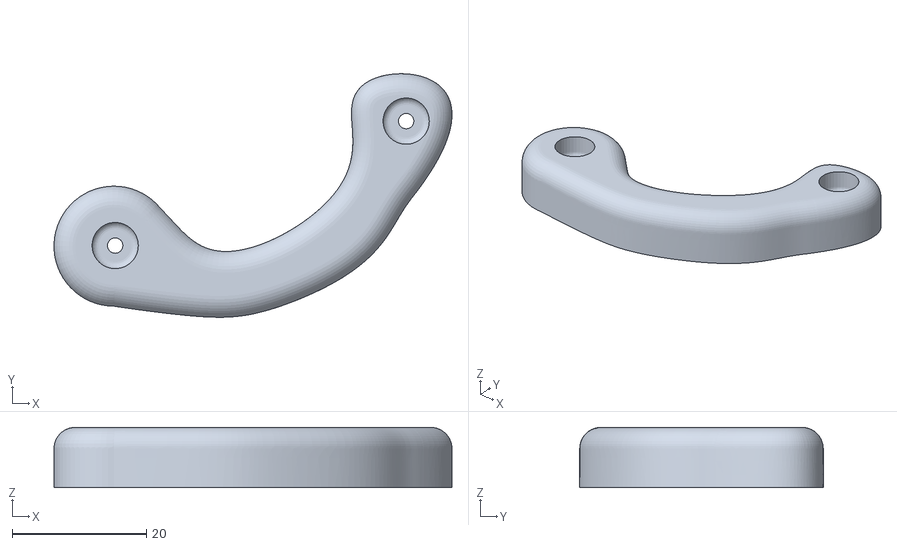
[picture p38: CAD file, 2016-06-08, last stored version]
quadruped/W4lker-master/stl/femur3.stl
59.4 x 36.3 x 9.00

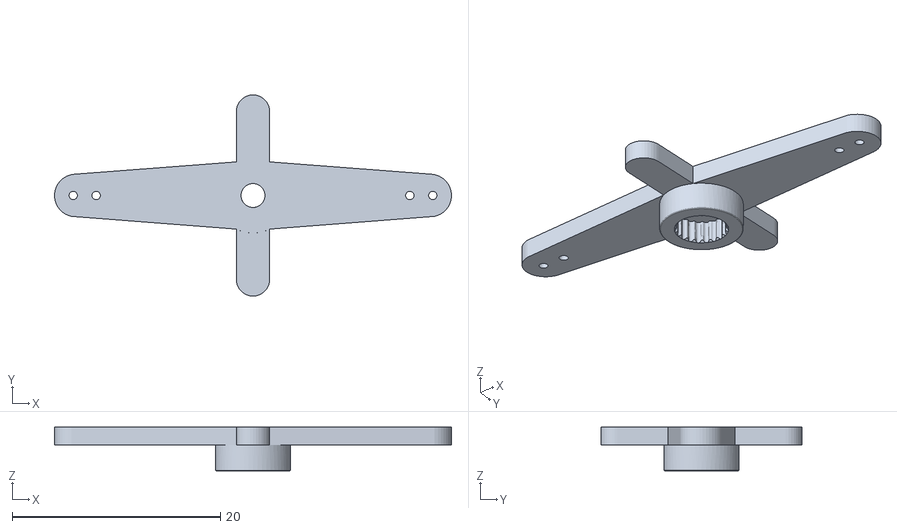
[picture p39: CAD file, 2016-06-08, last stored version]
quadruped/W4lker-master/stl/tg9 horn - Copy.stl
38.1 x 19.3 x 4.20

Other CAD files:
hardware/openscad/stl/test.obj
hardware/openscad/stl/u-frame.stl
quadruped/robotis/hardware/parts.scad
hardware/parts.scad
hardware/openscad/parts.scad
hardware/stl/test.obj
hardware/stl/u-frame.stl
quadraped/vrep/stl/tg9.stl
quadruped/W4lker-master/stl/tg9.stl
quadruped/robotis/hardware/stl/test.obj
quadruped/robotis/hardware/stl/u-frame.stl
quadruped/vrep/stl/tg9.stl

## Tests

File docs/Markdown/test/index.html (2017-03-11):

# Bill of Materials

#!/usr/bin python

# get stuff
import os

x = 3+4
ls = os.ls
for i in range(9):
    if i%4 == 0:
        print('ls:', ls)

\(v(t) = v_0 + \frac{1}{2}at^2\)

\(\gamma = \frac{1}{\sqrt{1 - v^2/c^2}}\)

\(\exists x \forall y (Rxy \equiv Ryx)\)

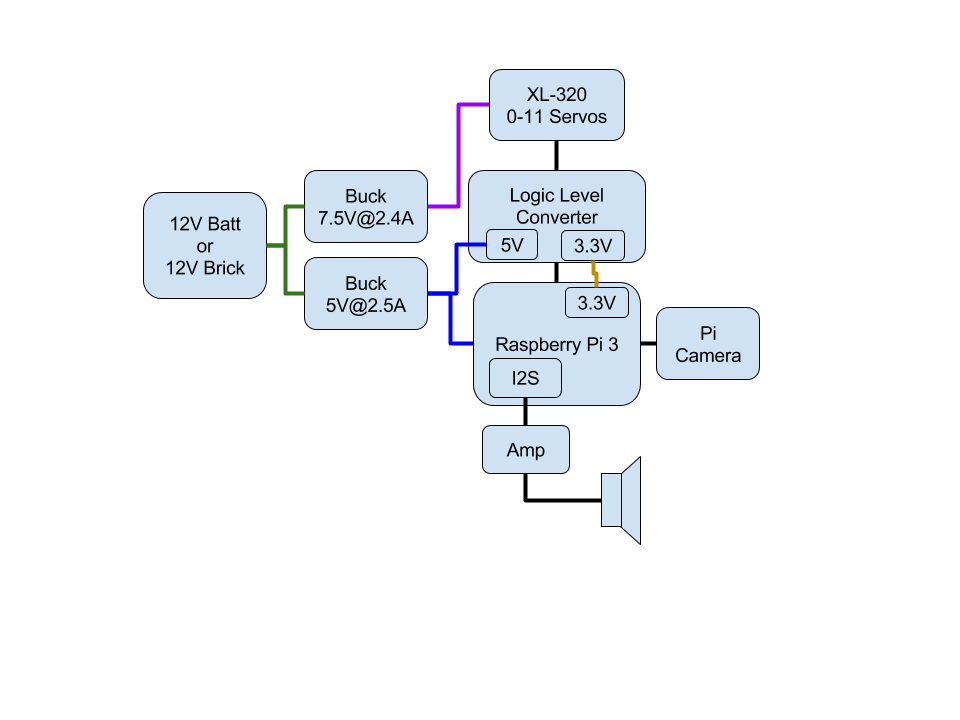
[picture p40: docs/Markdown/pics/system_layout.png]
system layout


system layout

### Raspberry Pi

I am currently using a 1.2 GHz quad core RPi 3 (https://www.adafruit.com/products/3055) (ARMv8) as the main board running the lite version of Raspbian. It has on-board:

- 802.11n Wifi
- Bluetooth 4.1 BLE

However, I have done a little testing and it looks like the Pi Zero might be powerful enough to do the job too. When I get more time, I will investigate it more.

### Pi Camera

PiCamera (https://www.adafruit.com/products/3099) is used to stream images.

### 3D Models

The 3d printer models (stl format) come from the following sources:

- Legs (https://github.com/mogillc/nico) which are the coxa, femur, and tibia
- Misc brackets I made using OpenScad (http://www.openscad.org/)

### Cost

Here is a parts list of key components that I am using. I am not listing wires, bread boards, cables, etc. Also note, I have rounded up the costs (i.e., $4.95 => $5). Also, lot of the body is 3d printed, the costs for that are not shown here.

Part | Source | Number | Item Cost | Sum | Notes
RPi v3 | Adafruit (https://www.adafruit.com) | 1 | $40 | $40 | Main board, has wifi and bluetooth already
Pi Camera | Adafruit (https://www.adafruit.com) | 1 | $30 | $30 | 8 Mpixel
5V, 5A Buck Converter (D24V22F5) | Pololu (https://www.pololu.com) | 1 | $10 | $10 | For powering the RPi
7.5V, 2.4A Buck Converter (D24V22F7) | Pololu (https://www.pololu.com) | 1 | $10 | $10 | For powering the xl-320
Dynamixel xl-320 smart servo | RobotShop (https://www.robotshop.com) | 12 | $22 | $264
PS4 Controller | Walmart (http://www.walmart.com) | 1 | $54 | $54
Micro SD (32 GB) | Walmart (http://www.walmart.com) | 1 | $12 | $12 | Raspbian
74LS241 | | 1 | $1 | $1 | Used to convert the RPi's RS232 into a RS485 port
Small signal MOSFET | | 1 | $1 | | Used for 3.3V to 5V conversion
12V, 5A Wall Power Adaptor | Pololu (https://www.pololu.com) | 1 | $15 | $15 | So I don't have to always run off batteries

<a rel="license" href="http://creativecommons.org/licenses/by-sa/4.0/">
    
</a>
<br />This work is licensed under a <a rel="license" href="http://creativecommons.org/licenses/by-sa/4.0/">Creative Commons Attribution-ShareAlike 4.0 International License</a>.

# History

Originally, this used toy RC servos (9 g's), they didn't work that great.

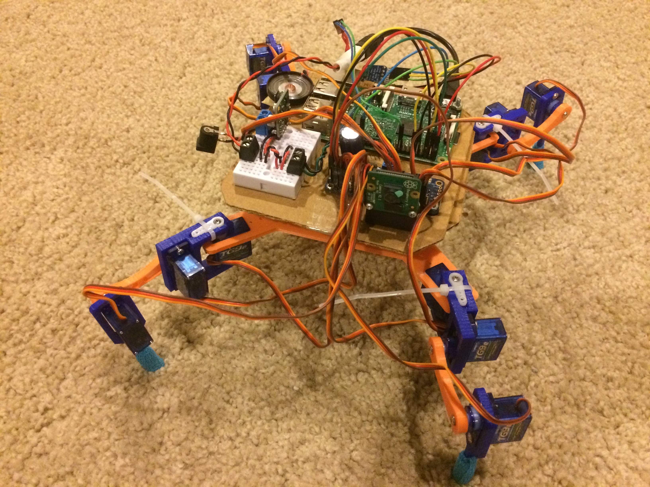
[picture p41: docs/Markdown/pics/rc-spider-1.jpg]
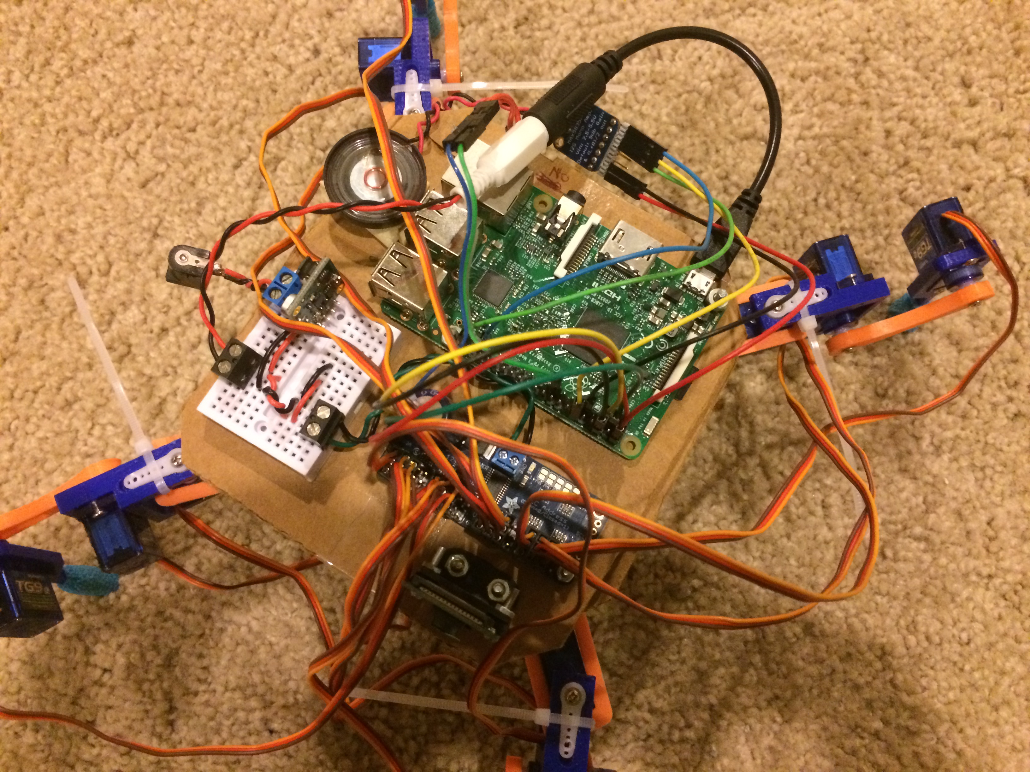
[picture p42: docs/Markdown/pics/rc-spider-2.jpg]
 

<a rel="license" href="http://creativecommons.org/licenses/by-sa/4.0/">
    
</a>
<br />This work is licensed under a <a rel="license" href="http://creativecommons.org/licenses/by-sa/4.0/">Creative Commons Attribution-ShareAlike 4.0 International License</a>.

Name: mcp23017 Info: Configures the MCP23017 I2C GPIO expander Load: dtoverlay=mcp23017,= Params: gpiopin Gpio pin connected to the INTA output of the MCP23017 (default: 4)

    addr                    I2C address of the MCP23017 (default: 0x20)

Name: i2s-gpio28-31 Info: move I2S function block to GPIO 28 to 31 Load: dtoverlay=i2s-gpio28-31 Params:

Name: i2c1-bcm2708 Info: Enable the i2c_bcm2708 driver for the i2c1 bus Load: dtoverlay=i2c1-bcm2708,= Params: sda1_pin GPIO pin for SDA1 (2 or 44 - default 2) scl1_pin GPIO pin for SCL1 (3 or 45 - default 3) pin_func Alternative pin function (4 (alt0), 6 (alt2) - default 4)

Name: i2c-rtc Info: Adds support for a number of I2C Real Time Clock devices Load: dtoverlay=i2c-rtc,= Params: ds1307 Select the DS1307 device

    ds1339                  Select the DS1339 device

    ds3231                  Select the DS3231 device

    mcp7940x                Select the MCP7940x device

    mcp7941x                Select the MCP7941x device

    pcf2127                 Select the PCF2127 device

    pcf8523                 Select the PCF8523 device

    pcf8563                 Select the PCF8563 device

    trickle-resistor-ohms   Resistor value for trickle charge (DS1339-only)

    wakeup-source           Specify that the RTC can be used as a wakeup
                            source

Name: i2c-pwm-pca9685a Info: Adds support for an NXP PCA9685A I2C PWM controller on i2c_arm Load: dtoverlay=i2c-pwm-pca9685a,= Params: addr I2C address of PCA9685A (default 0x40)

Name: i2c-mux Info: Adds support for a number of I2C bus multiplexers on i2c_arm Load: dtoverlay=i2c-mux,= Params: pca9542 Select the NXP PCA9542 device

    pca9545                 Select the NXP PCA9545 device

    pca9548                 Select the NXP PCA9548 device

    addr                    Change I2C address of the device (default 0x70)

Name: i2c-gpio Info: Adds support for software i2c controller on gpio pins Load: dtoverlay=i2c-gpio,= Params: i2c_gpio_sda GPIO used for I2C data (default "23")

    i2c_gpio_scl            GPIO used for I2C clock (default "24")

    i2c_gpio_delay_us       Clock delay in microseconds
                            (default "2" = ~100kHz)

# Documentation

This is still a work in progress

This documentation is broken up into two types:

- Static markdown files
- Interactive python files (Jupyter notebooks)

Since the software is written in python, iPhython (or now Jupyter (http://jupyter.org/)) is used for interactive documentation. Take a look at the docs (https://github.com/walchko/WalkingEye/tree/master/docs/ipython) folder. The ipython files are where some of the development (e.g., gait, forward/inverse kinematics, etc) takes place before it is tranferred into the python code.

When viewing the notebooks on github.com, they are static, but if you download them and have Jupyter installed, they are interactive and pretty cool.

## Index

- Software
- Hardware
- History

<a rel="license" href="http://creativecommons.org/licenses/by-sa/4.0/">
    
</a>
<br />This work is licensed under a <a rel="license" href="http://creativecommons.org/licenses/by-sa/4.0/">Creative Commons Attribution-ShareAlike 4.0 International License</a>.

# Software

## PyGecko

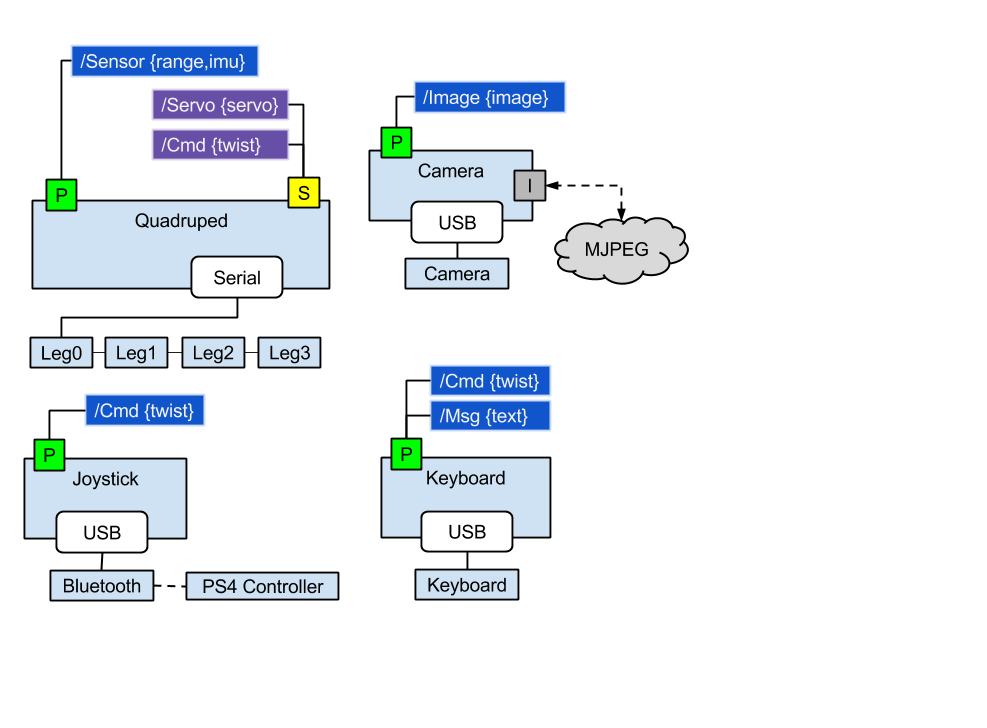
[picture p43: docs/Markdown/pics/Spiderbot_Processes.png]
Spiderbot_Processes


Spiderbot_Processes

This uses PyGecko (https://github.com/walchko/pygecko) (or ROS (http://www.ros.org) if you write the interface). PyGecko is a simple ROS like system written in python so it should run on anything python runs on.

pip install pygecko

Follow the other installation instructions for pygecko, will requires ZeroMQ (http://zeromq.org/) and some other libraries to be installed to work.

Since pygecko (like ROS) is based on the idea of many simple/modular processes, there is a launch.py file you run which will launch all of the necessary processes to get the robot running. If you don't need or want everything, you can just comment out what you don't need.

## pyXL320

This software requires pyxl320 (https://pypi.python.org/pypi/pyxl320) to work with the smart servos. You can install it with:

pip install pyxl320

Since all of the leg servos are on the same RS845 bus, you will need to use set_id to assign an id number to each servo BEFORE you hook them all together. To see how to use it, type:

set_id --help

## Other External Libraries

pip install adafruit-lsm303

## Tests

nose is used for unit tests ... just run nosetests -vs *.py.

## Low Level Quadruped Driver

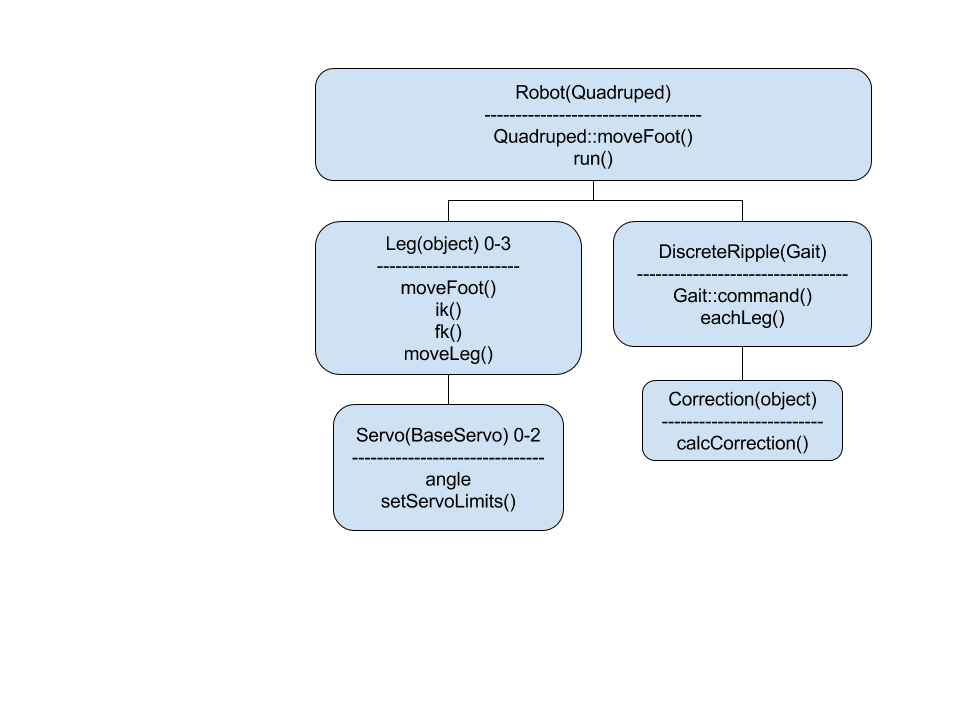
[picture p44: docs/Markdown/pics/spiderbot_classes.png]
spiderbot classes


spiderbot classes

The class diagram only shows the main classes and important functions, there is more. If you look in the quadruped folder, it contains the low level driver:

- Robot.py - main code to get things going ... adapt this to your needs.
- Quadruped.py - basic wrapper around leg and gait algorithms
- Leg.py - forward/reverse kinematics
- Gait.py - syncronization of how the 4 legs walk
- Servo.py - talks to the XL-320 smart servos
- ahrs - tilt compensated compass which gives roll, pitch, heading

<a rel="license" href="http://creativecommons.org/licenses/by-sa/4.0/">
    
</a>
<br />This work is licensed under a <a rel="license" href="http://creativecommons.org/licenses/by-sa/4.0/">Creative Commons Attribution-ShareAlike 4.0 International License</a>.

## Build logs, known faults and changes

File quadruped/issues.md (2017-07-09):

# Issues

- I don't think I am move the the diagonal feet. I am moving all 4 legs at a time ... issue?
    - I don't think so, I think I am thinking about it wrong ... gait handles it
- syncWrite is broken

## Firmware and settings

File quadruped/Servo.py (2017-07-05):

#!/usr/bin/env python
##############################################
# The MIT License (MIT)
# Copyright (c) 2016 Kevin Walchko
# see LICENSE for full details
##############################################

from __future__ import print_function
from __future__ import division
import logging
from pyxl320 import Packet
from pyxl320.Packet import makeSyncAnglePacket
# from pyxl320 import DummySerial
from pyxl320 import xl320

logger = logging.getLogger(__name__)


def makeBulkAnglePacket(info):
	"""
	Write bulk angle information to servos.

	info = [[ID, angle], [ID, angle], ...]
	"""
	addr = Packet.le(xl320.XL320_GOAL_POSITION)
	data = []
	for pkt in info:
		data.append(pkt[0])  # ID
		data.append(addr[0])  # LSB
		data.append(addr[1])  # MSB
		data.append(2)
		data.append(0)
		angle = Packet.le(int(pkt[1]/300*1023))
		data.append(angle[0])  # LSB
		data.append(angle[1])  # MSB

	ID = xl320.XL320_BROADCAST_ADDR
	instr = xl320.XL320_BULK_WRITE
	pkt = Packet.makePacket(ID, instr, None, data)  # create packet

	# print(pkt)
	return pkt


# I don't like global variables, but I don't know how else to have one array
# shared by all servos and have one simple class method to push updates
gBulkData = []
gSyncData = []  # this is much less data than bulk


class ServoBase(object):
	"""
	I might reverse these classes, so i can combine RC and Robotis servos
	ServoBase
	|  angle()
	|  limits()
	+- RCServo
		|  servo things
	+- RobotisServo
		|  bulkWrite
	"""
	ser = None
	bulkServoWrite = False
	syncServoWrite = False
	# bulkData = [0]

	def __init__(self):
		# just put a dummy serial here, because testing needs it in the angle setter
		if self.ser is None:
			# self.ser = DummySerial('test')
			raise Exception('ServoBase::__init__() no serial port')
		# pass

	# def setSerial(self, serialObj):
	# 	self.ser = serialObj

	@staticmethod
	def bulkWrite(ser):
		if ser is None:
			raise Exception('bulkWrite no serial port')
		print('Servo::bulkWrite()')
		global gBulkData
		pkt = makeBulkAnglePacket(gBulkData)
		ser.write(pkt)
		gBulkData = []  # clear global

	@staticmethod
	def syncWrite(ser):
		if ser is None:
			raise Exception('syncWrite no serial port')
		print('Servo::syncWrite()')
		global gSyncData
		print('gSyncData', gSyncData)
		pkt = makeSyncAnglePacket(gSyncData)
		print('pkt', pkt)
		ser.write(pkt)
		ser.write(pkt)
		gSyncData = []

	def write(self):
		if self.bulkServoWrite:
			self.bulkWrite(self.ser)
		elif self.syncServoWrite(self.ser):
			self.syncWrite(self.ser)
		else:
			raise Exception('ServoBase::write() not bulk or sync')


class Servo(ServoBase):
	"""
	Keeps info for servo and commands their movement.
	angles are in degrees

				0
	-150 ------ + ------- 150  kinematics (servo_k)
				150
		0 ------ + ------- 300  real servo (servo_r)

	servo_k commands are between -150 and 150 degrees, with 0 deg being center

	servo to kinematics: servo_r = servo_k + 150
	kinematics to servo: servo_k = servo_r - 150
	"""
	_angle = 0.0  # current angle
	_offset = 150.0  # angle offset default, see above for explaination
	minAngle = -150.0
	maxAngle = 150.0
	ID = 0

	def __init__(self, ID):
		"""
		limits [angle, angle] - [optional] set the angular limits of the servo to avoid collision
		"""
		ServoBase.__init__(self)
		self.ID = ID
		self.setServoLimits(150.0, -150.0, 150.0)  # defaults: offset, min, max

	@property
	def angle(self):
		"""
		Returns the current servo angle
		"""
		return self._angle

	@angle.setter
	def angle(self, angle):
		"""
		Sets the servo angle and clamps it between [limitMinAngle, limitMaxAngle].
		It also commands the servo to move.
		"""

		# saturates the angle if it is outside of the limits
		if self.minAngle > angle > self.maxAngle:
			# raise Exception('@angle.setter {} > {} > {}'.format(self.minAngle, angle, self.maxAngle))
			print('@angle.setter error {} > {} > {}'.format(self.minAngle, angle, self.maxAngle))

			if self.minAngle > angle:
				angle = self.minAngle
			elif self.maxAngle < angle:
				angle = self.maxAngle

			print('@angle.setter now {}'.format(angle))

		# print('servo[{}]: bulkWrite {}'.format(self.ID, self.bulkServoWrite))

		# only send a pkt if there is a change
		if self._angle != angle:
			self._angle = angle
			# servos are centered at 150 deg, but offset can change
			# print(self.ID, angle, angle + self._offset)

			if self.syncServoWrite:
				# global gBulkData
				# gBulkData.append([self.ID, angle + self._offset])
				gSyncData.append([self.ID, angle + self._offset])
				# self.bulkData.append([self.ID, angle + self._offset])
				# print('servo[{}]: bulkWrite {}'.format(self.ID, gBulkData))
			elif self.bulkServoWrite:
				# global gBulkData
				gBulkData.append([self.ID, angle + self._offset])
				# gSyncData.append([self.ID, angle + self._offset])
				# self.bulkData.append([self.ID, angle + self._offset])
				# print('servo[{}]: bulkWrite {}'.format(self.ID, gBulkData))
			else:
				pkt = Packet.makeServoPacket(self.ID, angle + self._offset)
				self.ser.sendPkt(pkt)
				# print('sent angle {} [{}]'.format(angle, angle + self._offset))

	def setServoLimits(self, offset, minAngle, maxAngle):
		"""
		sets maximum and minimum achievable angles. Remeber, the limits have to
		be within the servo range of [0, 180] ... anything more of less won't
		work unless your change setServoRangleAngle() to something other than
		0 - 180.

		in:
			minAngle - degrees
			maxAngle - degrees
		"""
		if minAngle > maxAngle:
			raise Exception("Servo::setServoLimits: min angle > max angle")

		self._offset = offset
		self.minAngle = minAngle
		self.maxAngle = maxAngle

		# # pktmax, pktmin = Packet.makeServoLimits(self.ID, maxAngle, minAngle)
		# angle = int(maxAngle/300.0*1023)
		# pkt = Packet.makeWritePacket(self.ID, xl320.XL320_CCW_ANGLE_LIMIT, Packet.le(angle))
		# ser.write(pkt)
		# # # ser.read()
		# angle = int(minAngle/300.0*1023)
		# pkt = Packet.makeWritePacket(self.ID, xl320.XL320_CW_ANGLE_LIMIT, Packet.le(angle))
		# ser.write(pkt)
		# # ser.read()

		# if 0:
		# 	# Example: kinematics only allow a servo between -180 and 0
		# 	# min -180
		# 	# max 0
		# 	# offset 240  <-- a real servo angle of 240 is a kinematic angle of 0
		# 	# limits = [-180+240, 0+240] = [60, 240]  <-- these are real servo angles
		# 	pkt = Packet.makeServoMinLimitPacket(self.ID, minAngle+self._offset)
		# 	self.ser.sendPkt(pkt)
		# 	pkt = Packet.makeServoMaxLimitPacket(self.ID, maxAngle+self._offset)
		# 	self.ser.sendPkt(pkt)


if __name__ == "__main__":
	print('Hello space cowboy!')

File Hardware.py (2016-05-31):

#!/usr/bin/env python
#
# by Kevin J. Walchko 26 Aug 2014
#
# Log:
# 12 Oct 14 Broke out into its own file
#

import time
# import datetime as date
import multiprocessing as mp
import logging
import IMU.MotorDriver as md
import RPi.GPIO as GPIO  # IR

import lib.zmqclass as zmq
import lib.Messages as Msg
import lib.FileStorage as Fs

# def test():
# 	import time
# 	mmd = md.MotorDriver(17,18,22,23)
#
# 	go  = {'dir': MotorDriver.FORWARD, 'duty': 50}
# 	rev = {'dir': MotorDriver.REVERSE, 'duty': 100}
# 	stp = {'dir': MotorDriver.REVERSE, 'duty': 0}
#
# 	mmd.setMotors(go,go,go,go)
# 	time.sleep(10)
# 	mmd.setMotors(rev,rev,rev,rev)
# 	time.sleep(10)
# 	mmd.setMotors(go,stp,go,stp)
# 	time.sleep(10)
# 	mmd.setMotors(stp,rev,stp,rev)
# 	time.sleep(10)
# 	mmd.allStop()

# class DigitalIR(object):
# 	"""
# 	Read IR sensors on digital inputs
#
# 	Pololu sds01a 0-5 cm pwr 3V output max 3V
# 	Sharp xxx 0-15 cm pwr 5V output max 3V - digital gives 3 inch range
# 	"""
# 	def __init__(self, pins):
# 		GPIO.setwarnings(False)
# 		GPIO.setmode(GPIO.BCM)
# 		for p in pins: GPIO.setup(p, GPIO.IN)
# 		self.pins = pins
#
# 	def read(self):
# 		ir = []
# 		for p in pins: ir.append( GPIO.input(p) )
# 		return ir


class RobotHardwareServer(mp.Process):
	"""
	RobotHardwareServer handles incoming commands streamed from somewhere else.
	in: commands/etc
	out: sensor readings
	"""
	def __init__(self, host="localhost", port=9000):
		mp.Process.__init__(self)
		self.host = host
		self.port = port
		logging.basicConfig(level=logging.INFO)
		self.logger = logging.getLogger('robot')
# 		self.md = md.MotorDriver(11,12,15,16)
		self.md = None

	def createMotorCmd(dir, duty):
		return {'dir': dir, 'duty': duty}

	def soundCmd(self, cmd):
		self.logger.info(cmd)

	def parseMsg(self, msg):
		if 'quit' in msg:
			self.shutdown()
		elif 'cmd' in msg:
			cmd = msg['cmd']
			if 'm' in cmd:
				self.motorCmd(cmd)
			elif 's' in cmd:
				self.soundCmd(cmd)

	def __del__(self):
		self.md.allStop()

	def on_message(self, client, userdata, msg):
		print(msg.topic + ' ' + str(msg.payload))

	def shutdown(self):
		"""
		Needed?
		"""
		0

	def test(self):
		dt = 5
		go = {'dir': md.MotorDriver.FORWARD, 'duty': 10}
		rev = {'dir': md.MotorDriver.REVERSE, 'duty': 10}
		stp = {'dir': md.MotorDriver.REVERSE, 'duty': 10}

		self.md.setMotors(go, go, go, go)
		time.sleep(dt)
		self.md.setMotors(rev, rev, rev, rev)
		time.sleep(dt)
		self.md.setMotors(go, stp, go, stp)
		time.sleep(dt)
		self.md.setMotors(stp, rev, stp, rev)
		time.sleep(dt)
		self.md.allStop()

	def run(self):
		self.logger.info(str(self.name) + '[' + str(self.pid) + '] started on' +
			str(self.host) + ':' + str(self.port) + ', Daemon: ' + str(self.daemon))
		# p = Publisher((self.host,self.port))
		# self.pub = p.accept()
		# self.logger.info('Accepted connection: ')

		self.sub = zmq.Sub(['cmds'])
		self.pub = zmq.Pub()

		while True:
			time.sleep(0.05)  # 0.5 => 20Hz
			# get info
			msg = self.sub.recv()
# 			if msg:
# 				self.parseMsg( msg )
			self.test()


class NonHolonomic(RobotHardwareServer):
	def __init__(self, host="localhost", port=9000):
		RobotHardwareServer.__init__(self, host, port)
		self.md = md.MotorDriver(11, 12)  # FIXME: 20160528 why these two pins?

	def motorCmd(self, cmd):
		self.logger.info(cmd)
		self.md.setMotors(cmd)


class Holonomic(RobotHardwareServer):
	def __init__(self, pinA=11, pinB=12, pinC=15, pinD=16):
		RobotHardwareServer.__init__(self)
		self.md = md.MotorDriver(pinA, pinB, pinC, pinD)

	def motorCmd(self, cmd):
		self.logger.info(cmd)
		self.md.setMotors(cmd)


if __name__ == '__main__':
	c = Holonomic()
	c.run()

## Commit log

2014-09-25 re-org, added sound and imu
    [robot.yaml]
2014-09-29 don't track latex processing file crap
2014-10-06 wtf github ... you suck!
    [robot.yaml]
2014-10-12 sort of working
    hard to get the robot’s attention … maybe there is a better way?
2014-10-12 sort of works
    crashes when i run robot.py, i think there is an issue with pyaudio
    somehow????
    [robot.yaml]
2014-10-15 fixed time stamp in sensor readings
2014-11-12 sim and pic updates
    made a pygame simulation for the matrix led. also added some new pics
    to latex
2014-11-12 update
    I thought I completed the ZMQ transition, but I didn’t. This does it
    along with re-architecting it.
    [zmqclass.py]
2015-07-26 motor mod
2015-07-26 motors working
2016-05-16 creating standard camera file
2016-05-24 camera calibrate included
2016-05-25 camera cal update
2016-06-08 updated docs, put in vrep example
    [base3 filet 2.stl, femur3.stl, shoulder_supports.stl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]
2016-07-02 servos working?
2016-07-02 servo test
2016-10-06 clean up
    [base3 filet 2.stl, femur3.stl, femur_v_2.stl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]
2016-11-19 major re-org ... only xl-320 quadruped now
    ok, i finally split out my different robots into their own
    repositories. I eventually plan to try to merge the robots xl-320 servo
    and rc servo robots together, but i am going to focus on the xl-320’s
    for now because they are super cool!
    [femur_v_2.stl, leg.stl, parts.scad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]
2016-11-21 update
    something wrong with gait, but mostly works
    [femur_SLA.STL, frame_adaptor.stl, leg.stl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]
2016-11-25 fix CM offset issue
    [Robot.py]
2016-11-30 update
    need to fix cm issue … screws something up
    [Robot.py]
2016-12-31 camera working
2017-03-13 more updates and refactor
    Array message doesn’t work right for some reason
    [ball_tracker.py, camera_server.py, face_detector.py]
2017-05-07 power jpg update
2017-07-04 print servo info

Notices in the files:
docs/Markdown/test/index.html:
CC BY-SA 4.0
